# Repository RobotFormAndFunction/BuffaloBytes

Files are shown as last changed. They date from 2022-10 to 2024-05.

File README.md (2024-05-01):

## Outline
- [Overview](https://github.com/RobotFormAndFunction/BuffaloBytes/edit/main/README.md#overview)
- [Hardware Specifications](https://github.com/RobotFormAndFunction/BuffaloBytes/edit/main/README.md#hardware-specifications)
- [Hardware Assembly](https://github.com/RobotFormAndFunction/BuffaloBytes#assembly)
- [Programming](https://github.com/RobotFormAndFunction/BuffaloBytes#programming)

# Overview
This repository contains Buffalo Bytes design, including the circuit board and mechanical hardware. The bill of materials and 3D design files are included. This README file details the hardware specifications and tutorials on getting started with the Buffalo Bytes platform.

The robot is presented in the the IEEE Robotics and Automation Letter article, [Buffalo Byte: A Highly Mobile and Autonomous Millirobot Platform](https://ieeexplore.ieee.org/document/10465605)

To cite:
```bibtex
@ARTICLE{Singh_2024,
  author={Singh, Shashwat and Truax, Reed and St.~Pierre, Ryan},
  journal={IEEE Robotics and Automation Letters}, 
  title={Buffalo Byte: A Highly Mobile and Autonomous Millirobot Platform}, 
  year={2024},
  volume={9},
  number={5},
  pages={4067-4074},
  keywords={Robots;Robot sensing systems;Legged locomotion;Wheels;Batteries;Wireless fidelity;Three-dimensional displays;Biomimetics;field robots;biologically-inspired robots;millirobot},
  doi={10.1109/LRA.2024.3375290}}
```

# Hardware Specifications
This section details the electrical and mechanical hardware used in the Buffalo Bytes platform.

## Electrical hardware
The custom PCB for Buffalo Bytes is detailed in [here](https://github.com/RobotFormAndFunction/BuffaloBytes/tree/main/ElectricalHardware), with the schematic of the board, Gerber files, and BOM (bill of materials). The microcontroller is an ESP8266x SoC (system-on-a-chip), which enables Wi-Fi, and general input/outputs. The summary of electrical hardware is below in the BOM. 

<details><summary>Bill of materials (BOM)</summary>

#### Passives

| Component | Value	| Quantity | Package size |
| :--- | --- | :---: | --- |
| Capacitor |	0.1 µF |	5 |	0603 |
| Capacitor |	8.6 pF |	1 |	0603 |
| Capacitor | 2.4 pF |	1 |	0603 |
| Capacitor |	10 µF |	3 |	0603 |
| Capacitor |	1 µF |	2 |	0603 |
| Capacitor |	5.6 pF |	2 |	0603 |
| Capacitor |	2.2 µF |	1 |	0603 |
| Capacitor |	220 pF |	1 |	0603 |
| Capacitor |	0.01 µF |	1 |	0603 |		
| Inductor | 1.5 nH |	1 |	0603 |		
| Resistor |	200 Ω |	1 |	0603 |
| Resistor |	12 kΩ |	5 |	0603 |
| Resistor |	1 kΩ |	1 |	0603 |
| Resistor |	4.7 kΩ |	4 |	0603 |		
| LED |	Red |	1 |	0603 |

#### Electronics

| Part | Part Number	| Quantity | Package size |
| :--- | --- | :---: | --- |
| Antenna |	AN9520-245 |	1 |	ANT-SMD_L9.5-W2.1 |
| Crystal - 26 MHz | ECS-260 |	1 |	4-SMD, no lead |
| MCU |	ESP8266x |	1 |	QFN-32 |
| Motor driver |	DRV8833 |	1 |	TSSOP-16 |
| IMU |	MPU6050 |	1 |	QFN-24 |
| LDO Voltage regulator |	TPS7A0533PDBZR | 1 |	SOT-23 |	
| Flash memory | ZB25VQ80 | 1 | SOIC-8 |
</details>

# Assembly
The exploded view of a Buffalo Byte is shown below.

<p align="center">
Exploded View of Buffalo Bytes
</p>

First, the custom PCB needs to be populated (details in [Electrical Hardware](https://github.com/RobotFormAndFunction/BuffaloBytes/tree/main/ElectricalHardware)), and all of the mechanical hardware sourced, printed, and molded (details in [Mechanical Hardware](https://github.com/RobotFormAndFunction/BuffaloBytes/tree/main/MechanicalHardware)).

Each Buffalo Byte is assembled by sliding the motors into the chassis, attached the actuated wheels to the motors, and unactuated wheels to carbon fiber axles. The molded treads are wrapped around each actuated-unactuated wheel pair. The motor wires are connected to the custom PCB, and the battery connected to the PCB as well. Kapton tape is applied around the body to secure all parts. 

## Programming

To Buffalo Bytes Boards has 8 headers that goes directly into female headers of ESP8266 burning fixture to upload either the bootloader or code through serial communication. A USB-ASP programmer can also be used to do the same task, though the burning fixture is recommended. 

<p align="center">
ESP8266 Burning fixture
</p>

The board can be bootloaded with both Arduino and MicroPython to make software development easy. In this work, the board is flashed with the Arduino bootloader, and the Arduino IDE was used for software development. Alternatively, the board also enables wireless programming using Wi-Fi. To do this, a base script must be first uploaded through a serial connection, then additional programs can be sent via Wi-Fi.

To bootload Micropython firmware on the board, we downloaded and uploaded the latest micropython firmware from official micropython website. [(https://micropython.org/download/esp8266-1m/)](https://micropython.org/download/esp8266-1m/).

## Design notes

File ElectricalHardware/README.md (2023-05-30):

# Electrical hardware
The custom PCB of for Buffalo Bytes is shown below, with the top (A) and bottom (B). 

<p align="center">
PCB_annotate
</p>

The schematic of the board is shown [here](https://github.com/RobotFormAndFunction/BuffaloBytes/blob/main/ElectricalHardware/Buffalo_Bytes_schematic.pdf), and Gerber files [here](https://github.com/RobotFormAndFunction/BuffaloBytes/blob/main/ElectricalHardware/Gerber_PCB_BuffaloBytes.zip).

## Bill of materials (BOM)

### Passives

| Component | Value	| Quantity | Package size |
| :--- | --- | :---: | --- |
| Capacitor |	0.1 µF |	5 |	0603 |
| Capacitor |	8.6 pF |	1 |	0603 |
| Capacitor | 2.4 pF |	1 |	0603 |
| Capacitor |	10 µF |	3 |	0603 |
| Capacitor |	1 µF |	2 |	0603 |
| Capacitor |	5.6 pF |	2 |	0603 |
| Capacitor |	2.2 µF |	1 |	0603 |
| Capacitor |	220 pF |	1 |	0603 |
| Capacitor |	0.01 µF |	1 |	0603 |		
| Inductor | 1.5 nH |	1 |	0603 |		
| Resistor |	200 Ω |	1 |	0603 |
| Resistor |	12 kΩ |	5 |	0603 |
| Resistor |	1 kΩ |	1 |	0603 |
| Resistor |	4.7 kΩ |	4 |	0603 |		
| LED |	Red |	1 |	0603 |

### Electronics

| Part | Part Number	| Quantity | Package size |
| :--- | --- | :---: | --- |
| Antenna |	AN9520-245 |	1 |	ANT-SMD_L9.5-W2.1 |
| Crystal - 26 MHz | ECS-260 |	1 |	4-SMD, no lead |
| MCU |	ESP8266x |	1 |	QFN-32 |
| Motor driver |	DRV8833 |	1 |	TSSOP-16 |
| IMU |	MPU6881 |	1 |	QFN-24 |
| LDO Voltage regulator |	TPS7A0533PDBZR | 1 |	SOT-23 |	
| Flash memory | ZB25VQ80 | 1 | SOIC-8 |

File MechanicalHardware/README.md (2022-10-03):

# Mechanical hardware

The mechanical hardware of the Buffalo Bytes requires both commercial off-the-shelf (COTS) hardware and custom hardare. The COTS hardware is listed below in the bill of materials (BOM) and the STL files for the custom hardware in this repository. 

## COTS hardware
| Component| Quantity | Comment |
| :--- | :---: | --- |
| Two-stage (26:1) planetary gearmotor |	2 |	Available from Pololu |
| LiPo Battery (3.7 V @ 100 mAh) |	1 |	Available on Amazon |
| Carbon fiber rod | 1 | 1 mm diameter cut to size |
| Silicone polymer | 1 | DragonSkin 10 from Smooth-On |

## Custom hardware
One copy of the [chassis.stl](https://github.com/RobotFormAndFunction/BuffaloBytes/blob/main/MechanicalHardware/chassis.stl) and four copies of the [wheel.stl](https://github.com/RobotFormAndFunction/BuffaloBytes/blob/main/MechanicalHardware/wheel.stl) files need to be printed on an SLA printer. We used an AnyCubic Mono SE printer. The parts were printed according to the directions for the printer, and post-processed by rinsing with IPA, and cured in a UV light chamber. Other 3D printing options may require different processing.

The [tread_mold.stl](https://github.com/RobotFormAndFunction/BuffaloBytes/blob/main/MechanicalHardware/tread_mold.stl) file was printed on an FDM printer, we used a Raise3D E2 printer. After printing, a two-part silicone rubber (DragonSkin 10) was mixed and poured into the mold and allowed to cure overnight.

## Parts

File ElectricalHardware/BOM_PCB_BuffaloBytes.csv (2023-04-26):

ID | Name | Designator | Footprint | Quantity | Manufacturer Part | Manufacturer | Supplier | Supplier Part | Price | Pins | 3DModel | Contributor | Frequency | link
1 | 8.6pF | C2 | C0603 | 1 |  |  |  |  |  | 2 | C0603_L1.6-W0.8-H0.8 | LCEDA_Lib |  | https://item.szlcsc.com/362304.html
2 | 2.4pF | C3 | C0603 | 1 |  |  |  |  |  | 2 | C0603_L1.6-W0.8-H0.8 | LCEDA_Lib |  | https://item.szlcsc.com/362304.html
3 | 10u | C10 | C0603 | 1 |  |  |  |  |  | 2 | C0603_L1.6-W0.8-H0.8 | LCEDA_Lib |  | https://item.szlcsc.com/362304.html
4 | 1uF | C16 | C0603 | 1 |  |  |  |  |  | 2 | C0603_L1.6-W0.8-H0.8 | LCEDA_Lib |  | https://item.szlcsc.com/362304.html
5 | 200 | R1 | R0603 | 1 |  |  |  |  |  | 2 | R0603 | LCEDA_Lib |  | https://www.mouser.in/datasheet/2/447/PYu_RT_1_to_0_01_RoHS_L_11-1669912.pdf
6 | 12k | R2,R4,R6,R5,R7 | R0603 | 5 |  |  |  |  |  | 2 | R0603 | LCEDA_Lib |  | https://www.mouser.in/datasheet/2/447/PYu_RT_1_to_0_01_RoHS_L_11-1669912.pdf
7 | 1k | R3,R8,R9 | R0603 | 3 |  |  |  |  |  | 2 | R0603 | LCEDA_Lib |  | https://www.mouser.in/datasheet/2/447/PYu_RT_1_to_0_01_RoHS_L_11-1669912.pdf
8 | TPS7A0533PDBZR | U4 | SOT-23-3_L2.9-W1.3-P1.90-LS2.4-BR | 1 | TPS7A0533PDBZR | TI(德州仪器) | LCSC | C2877921 | 0.077 | 3 | SOT-23-3P_L2.9-W1.3-H1.0-LS2.4-P0.95 | LCSC |  | https://www.diodes.com/assets/Package-Files/SOT23.pdf
9 | 1.27MM*4P排母 | MO | HDR-TH_4P-P1.27_1.27MM-4P | 1 | 1.27mm*4P排母 |  | LCSC | C9900006150 |  | 4 | HDR-TH_4P-P1.27_1.27MM-4P | LCSC |  | https://cn.bing.com/search?q=datasheet： 1.27mm*4P排母
10 | Molex white 2-pin | J1 | MOLEX PICOBLADE 2P SMD | 1 | Molex white 2-pin |  |  |  |  | 4 |  | Dror
11 | 1.5nH | L1 | L0603 | 1 |  |  |  |  |  | 2 | L0603_L1.6-W0.8-H0.5_BEAD | LCEDA_Lib |  | https://item.szlcsc.com/344093.html
12 | AN9520-245 | L3 | ANT-SMD_L9.5-W2.1 | 1 | AN9520-245 | Rainsun | LCSC | C99665 | 0.05 | 2 | ANT-SMD_L9.5-W2.1-H1.0 | 立创EDA官方封装库 |  | https://item.szlcsc.com/100880.html
13 | LED-0603_R | LED1 | LED0603_RED | 1 | 19-217/R6C-AL1M2VY/3T | EVERLIGHT(台湾亿光) | LCSC | C72044 | 0.003 | 2 | LED0603_Red | LCEDA_01
14 | ESP8266EX | U1 | QFN-32_L5.0-W5.0-P0.50-BL-EP3.7 | 1 | ESP8266EX | ESPRESSIF | LCSC | C77967 | 0.167 | 33 | QFN-32_L5.0-W5.0-H0.8-P0.50-BL-EP3.7 | lcsc | 2.4GHz | https://item.szlcsc.com/18002.html
15 | W25Q32JWSSIQ_C2980995 | U2 | SOIC-8_L5.3-W5.3-P1.27-LS8.0-BL | 1 | W25Q32JWSSIQ | WINBOND(华邦) | LCSC | C2980995 | 0.124 | 8 | SOIC-8_L5.3-W5.3-H1.9-LS7.9-P1.27 | LCSC |  | https://atta.szlcsc.com/upload/public/pdf/source/20210417/916358944D87095CD419D96946FBE847.pdf
16 | 10pF | C12,C8 | C0603 | 2 |  |  |  |  |  | 2 | C0603_L1.6-W0.8-H0.8 | LCEDA_Lib |  | https://item.szlcsc.com/362304.html
17 | 26MHz | X2 | CRYSTAL-SMD_4P-L1.6-W1.2-BL | 1 | X1E000251001400 | EPSON(爱普生) | LCSC | C1985224 | 0.057 | 4 | CRYSTAL-SMD_4P-L1.6-W1.2-BL | LCSC |  | https://atta.szlcsc.com/upload/public/pdf/source/20180822/C255986_1A5575095A8CA427CA557DB66E6B870C.pdf
18 | Presa PCB HARWIN, 10 vie, 2 file, passo 1.27mm, Foro passante | U5 | HEADER PTR 10X1,27 | 1 | M50-3530842 | M50-3000545 | RS-Online | 681-0692 |  | 10 |  | Marco Anfesi |  | https://it.rs-online.com/web/p/prese-pcb/6810692
19 | 10nF | C11 | C0603 | 1 |  |  |  |  |  | 2 | C0603_L1.6-W0.8-H0.8 | LCEDA_Lib |  | https://item.szlcsc.com/362304.html
20 | 0.1u | C1,C4,C18,C19 | C0603 | 4 |  |  |  |  |  | 2 | C0603_L1.6-W0.8-H0.8 | LCEDA_Lib |  | https://item.szlcsc.com/362304.html
21 | 10k | R12,R14,R15,R16 | R0603 | 4 |  |  |  |  |  | 2 | R0603 | LCEDA_Lib |  | https://www.mouser.in/datasheet/2/447/PYu_RT_1_to_0_01_RoHS_L_11-1669912.pdf
22 | MPU-6881_C468935 | R13 | QFN-24_L3.0-W3.0-P0.40-TL-EP | 1 | MPU-6881 | TDK InvenSense(应美盛) | LCSC | C468935 | 0.588 | 25 |  | LCSC |  | http://file1.dzsc.com/product/15/01/20/193739_103049784.pdf
23 | 10uF | C5,C17 | C0603 | 2 |  |  |  |  |  | 2 | C0603_L1.6-W0.8-H0.8 | LCEDA_Lib |  | https://item.szlcsc.com/362304.html
24 | 1u | C6 | C0603 | 1 |  |  |  |  |  | 2 | C0603_L1.6-W0.8-H0.8 | LCEDA_Lib |  | https://item.szlcsc.com/362304.html
25 | 2.2u | C9 | C0603 | 1 |  |  |  |  |  | 2 | C0603_L1.6-W0.8-H0.8 | LCEDA_Lib |  | https://item.szlcsc.com/362304.html
26 | 0.01u | C15 | C0603 | 1 |  |  |  |  |  | 2 | C0603_L1.6-W0.8-H0.8 | LCEDA_Lib |  | https://item.szlcsc.com/362304.html
27 | DRV8833CPWPR | U3 | TSSOP-16_L5.0-W4.4-P0.65-LS6.4-BL-EP-1 | 1 | DRV8833CPWPR | Texas Instruments | LCSC | C191171 | 0.868 | 17 | TSSOP-16_L5.0-W4.4-P0.65-LS6.4-BL-EP-1 | LCSC |  | https://www.ti.com/cn/lit/ds/symlink/drv8833c.pdf?ts=1631004531499

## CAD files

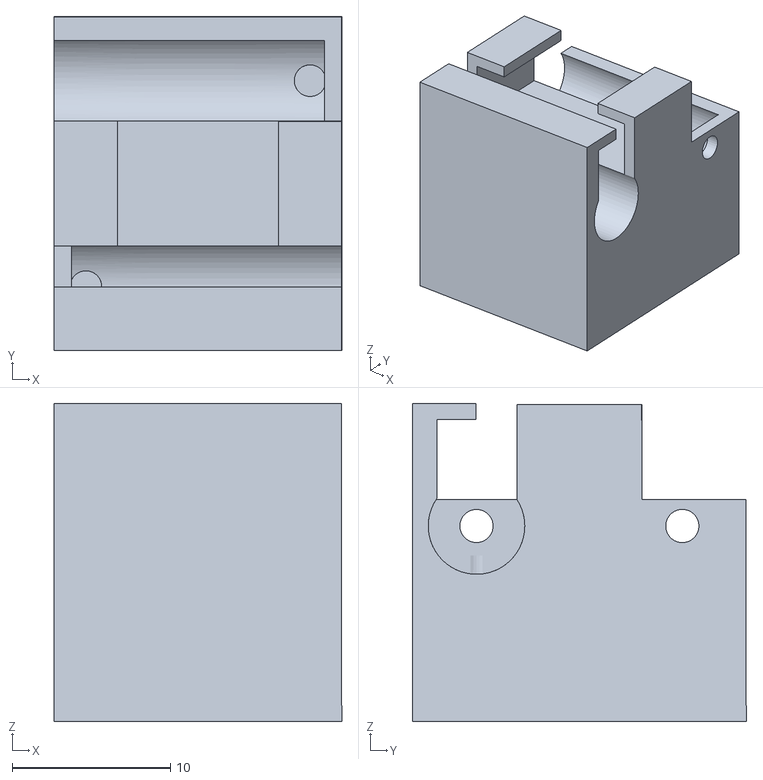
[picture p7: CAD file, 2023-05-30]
MechanicalHardware/NewChassis.stl
18.2 x 21.1 x 20.1

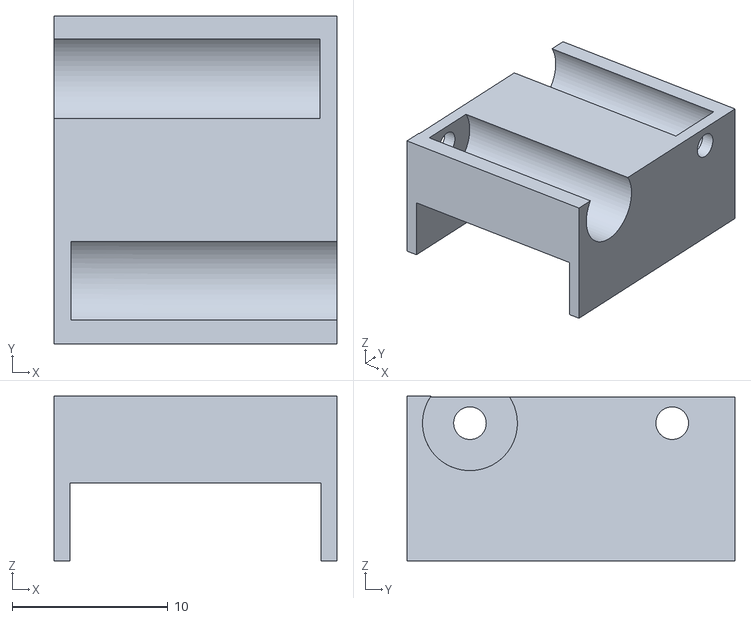
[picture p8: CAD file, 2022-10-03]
MechanicalHardware/chassis.stl
18.2 x 21.1 x 10.6

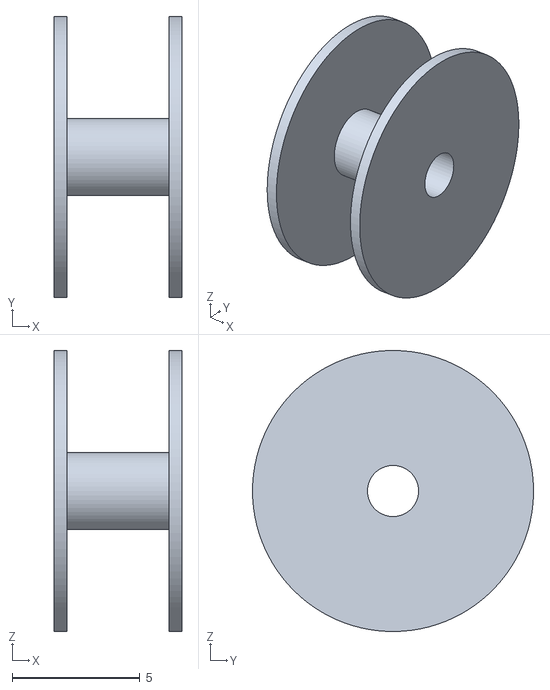
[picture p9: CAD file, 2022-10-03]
MechanicalHardware/wheel.stl
5.00 x 11.0 x 11.0

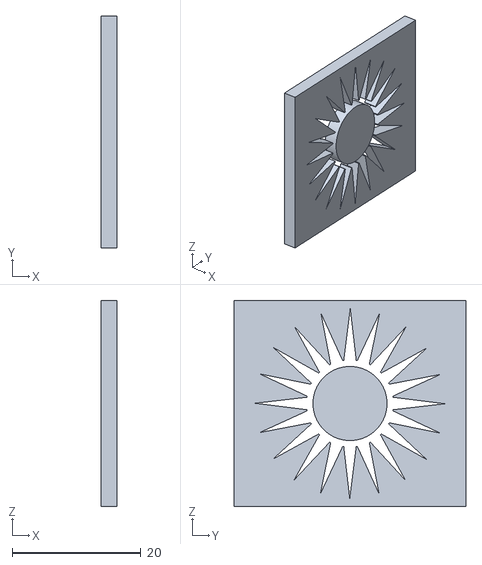
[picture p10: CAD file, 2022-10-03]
MechanicalHardware/tread_mold.stl
2.50 x 36.0 x 32.0

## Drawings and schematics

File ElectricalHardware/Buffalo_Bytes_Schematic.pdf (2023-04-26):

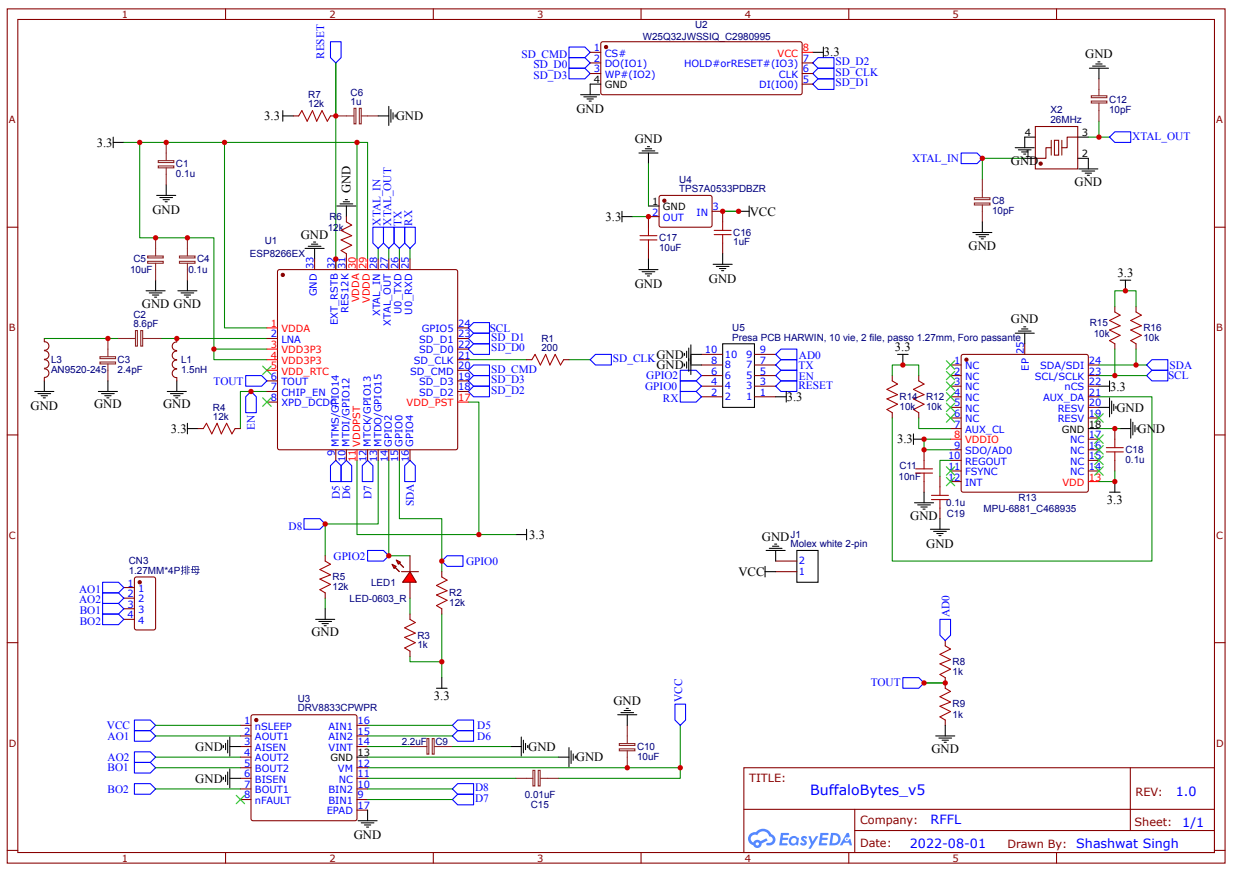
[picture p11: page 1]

Drawn By: Shashwat Singh

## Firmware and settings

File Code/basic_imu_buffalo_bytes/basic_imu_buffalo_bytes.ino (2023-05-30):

/***************************************************************************
* Example sketch for the MPU6500_WE library
*
* This sketch shows how to get acceleration, gyroscocope and temperature 
* data from the MPU6500. In essence, the difference to the MPU9250 is the
* missing magnetometer. The shall only show how to "translate" all other 
* MPU9250 example sketches for use of the MPU6500
* 
* For further information visit my blog:
*
* https://wolles-elektronikkiste.de/mpu9250-9-achsen-sensormodul-teil-1  (German)
* https://wolles-elektronikkiste.de/en/mpu9250-9-axis-sensor-module-part-1  (English)
* 
***************************************************************************/

#include <MPU6500_WE.h>
#include <Wire.h>
#define MPU6500_ADDR 0x69

/* There are several ways to create your MPU6500 object:
 * MPU6500_WE myMPU6500 = MPU6500_WE()              -> uses Wire / I2C Address = 0x68
 * MPU6500_WE myMPU6500 = MPU6500_WE(MPU6500_ADDR)  -> uses Wire / MPU6500_ADDR
 * MPU6500_WE myMPU6500 = MPU6500_WE(&wire2)        -> uses the TwoWire object wire2 / MPU6500_ADDR
 * MPU6500_WE myMPU6500 = MPU6500_WE(&wire2, MPU6500_ADDR) -> all together
 * Successfully tested with two I2C busses on an ESP32
 */
MPU6500_WE myMPU6500 = MPU6500_WE(MPU6500_ADDR);

void setup() {
  Serial.begin(115200);
  Wire.begin();
  if(!myMPU6500.init()){
    Serial.println("MPU6500 does not respond");
  }
  else{
    Serial.println("MPU6500 is connected");
  }
  
  /* The slope of the curve of acceleration vs measured values fits quite well to the theoretical 
   * values, e.g. 16384 units/g in the +/- 2g range. But the starting point, if you position the 
   * MPU6500 flat, is not necessarily 0g/0g/1g for x/y/z. The autoOffset function measures offset 
   * values. It assumes your MPU6500 is positioned flat with its x,y-plane. The more you deviate 
   * from this, the less accurate will be your results.
   * The function also measures the offset of the gyroscope data. The gyroscope offset does not   
   * depend on the positioning.
   * This function needs to be called at the beginning since it can overwrite your settings!
   */
  Serial.println("Position you MPU6500 flat and don't move it - calibrating...");
  delay(1000);
  myMPU6500.autoOffsets();
  Serial.println("Done!");
  
  /*  This is a more accurate method for calibration. You have to determine the minimum and maximum 
   *  raw acceleration values of the axes determined in the range +/- 2 g. 
   *  You call the function as follows: setAccOffsets(xMin,xMax,yMin,yMax,zMin,zMax);
   *  Use either autoOffset or setAccOffsets, not both.
   */
  //myMPU6500.setAccOffsets(-14240.0, 18220.0, -17280.0, 15590.0, -20930.0, 12080.0);

  /*  The gyroscope data is not zero, even if you don't move the MPU6500. 
   *  To start at zero, you can apply offset values. These are the gyroscope raw values you obtain
   *  using the +/- 250 degrees/s range. 
   *  Use either autoOffset or setGyrOffsets, not both.
   */
  //myMPU6500.setGyrOffsets(45.0, 145.0, -105.0);

  /*  You can enable or disable the digital low pass filter (DLPF). If you disable the DLPF, you 
   *  need to select the bandwdith, which can be either 8800 or 3600 Hz. 8800 Hz has a shorter delay,
   *  but higher noise level. If DLPF is disabled, the output rate is 32 kHz.
   *  MPU6500_BW_WO_DLPF_3600 
   *  MPU6500_BW_WO_DLPF_8800
   */
  myMPU6500.enableGyrDLPF();
  //myMPU6500.disableGyrDLPF(MPU6500_BW_WO_DLPF_8800); // bandwdith without DLPF
  
  /*  Digital Low Pass Filter for the gyroscope must be enabled to choose the level. 
   *  MPU6500_DPLF_0, MPU6500_DPLF_2, ...... MPU6500_DPLF_7 
   *  
   *  DLPF    Bandwidth [Hz]   Delay [ms]   Output Rate [kHz]
   *    0         250            0.97             8
   *    1         184            2.9              1
   *    2          92            3.9              1
   *    3          41            5.9              1
   *    4          20            9.9              1
   *    5          10           17.85             1
   *    6           5           33.48             1
   *    7        3600            0.17             8
   *    
   *    You achieve lowest noise using level 6  
   */
  myMPU6500.setGyrDLPF(MPU6500_DLPF_6);

  /*  Sample rate divider divides the output rate of the gyroscope and accelerometer.
   *  Sample rate = Internal sample rate / (1 + divider) 
   *  It can only be applied if the corresponding DLPF is enabled and 0<DLPF<7!
   *  Divider is a number 0...255
   */
  myMPU6500.setSampleRateDivider(5);

  /*  MPU6500_GYRO_RANGE_250       250 degrees per second (default)
   *  MPU6500_GYRO_RANGE_500       500 degrees per second
   *  MPU6500_GYRO_RANGE_1000     1000 degrees per second
   *  MPU6500_GYRO_RANGE_2000     2000 degrees per second
   */
  myMPU6500.setGyrRange(MPU6500_GYRO_RANGE_250);

  /*  MPU6500_ACC_RANGE_2G      2 g   (default)
   *  MPU6500_ACC_RANGE_4G      4 g
   *  MPU6500_ACC_RANGE_8G      8 g   
   *  MPU6500_ACC_RANGE_16G    16 g
   */
  myMPU6500.setAccRange(MPU6500_ACC_RANGE_2G);

  /*  Enable/disable the digital low pass filter for the accelerometer 
   *  If disabled the bandwidth is 1.13 kHz, delay is 0.75 ms, output rate is 4 kHz
   */
  myMPU6500.enableAccDLPF(true);

  /*  Digital low pass filter (DLPF) for the accelerometer, if enabled 
   *  MPU6500_DPLF_0, MPU6500_DPLF_2, ...... MPU6500_DPLF_7 
   *   DLPF     Bandwidth [Hz]      Delay [ms]    Output rate [kHz]
   *     0           460               1.94           1
   *     1           184               5.80           1
   *     2            92               7.80           1
   *     3            41              11.80           1
   *     4            20              19.80           1
   *     5            10              35.70           1
   *     6             5              66.96           1
   *     7           460               1.94           1
   */
  myMPU6500.setAccDLPF(MPU6500_DLPF_6);

  /* You can enable or disable the axes for gyroscope and/or accelerometer measurements.
   * By default all axes are enabled. Parameters are:  
   * MPU6500_ENABLE_XYZ  //all axes are enabled (default)
   * MPU6500_ENABLE_XY0  // X, Y enabled, Z disabled
   * MPU6500_ENABLE_X0Z   
   * MPU6500_ENABLE_X00
   * MPU6500_ENABLE_0YZ
   * MPU6500_ENABLE_0Y0
   * MPU6500_ENABLE_00Z
   * MPU6500_ENABLE_000  // all axes disabled
   */
  //myMPU6500.enableAccAxes(MPU6500_ENABLE_XYZ);
  //myMPU6500.enableGyrAxes(MPU6500_ENABLE_XYZ);
  delay(200);
}

void loop() {
  xyzFloat gValue = myMPU6500.getGValues();
  xyzFloat gyr = myMPU6500.getGyrValues();
  float temp = myMPU6500.getTemperature();
  float resultantG = myMPU6500.getResultantG(gValue);

  Serial.println("Acceleration in g (x,y,z):");
  Serial.print(gValue.x);
  Serial.print("   ");
  Serial.print(gValue.y);
  Serial.print("   ");
  Serial.println(gValue.z);
  Serial.print("Resultant g: ");
  Serial.println(resultantG);

  Serial.println("Gyroscope data in degrees/s: ");
  Serial.print(gyr.x);
  Serial.print("   ");
  Serial.print(gyr.y);
  Serial.print("   ");
  Serial.println(gyr.z);

  Serial.print("Temperature in °C: ");
  Serial.println(temp);

  Serial.println("********************************************");

  delay(1000);
}

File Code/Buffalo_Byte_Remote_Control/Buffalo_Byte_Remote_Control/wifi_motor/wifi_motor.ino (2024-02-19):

#include <ESP8266WiFi.h>
#include <WiFiClient.h>
#include <ESP8266WebServer.h>

// Replace with your network credentials
const char* ssid = "Aniket";         
const char* password = "1234567890";

ESP8266WebServer server(80);   //instantiate server at port 80 (http port)

String page = ""; //For the Web Server
String page2="";  //For updating Status of motor 1
String page3="";  //For updating status of motor 2
void setup(void)
{
  //the HTML of the web page
  page = "<center><h1>Motor Control Web Server</h1><body><p><a href=\"Forward\"><button>Forward</button></a><p><a href=\"Backward\"><button>Backward</button></a></p><p><a href =\"Left\"><button>Left</button></a>&nbsp;<a href=\"Stop\"><button>Stop</button></a><a href=\"Right\"><button>Right</button></a></p></body></center>";
  pinMode(14, OUTPUT);   // inputs for motor 1
  pinMode(12,OUTPUT);
  pinMode(13,OUTPUT);    // inputs for motor 2 
  pinMode(15,OUTPUT);
  pinMode(LED_BUILTIN,OUTPUT);  // For status of WiFi connection
  delay(1000);
  Serial.begin(115200);     
  WiFi.begin(ssid, password); //begin WiFi connection
  Serial.println("");

  // Wait for connection
  while (WiFi.status() != WL_CONNECTED) {
    delay(500);
    Serial.print(".");
  }
  digitalWrite(LED_BUILTIN,HIGH);     // when connected turns high
  Serial.println("");
  Serial.print("Connected to ");   
  Serial.println(ssid);
  Serial.print("IP address: ");
  Serial.println(WiFi.localIP());   //provides IP address
   server.on("/", [](){
    server.send(200, "text/html", page+page2);
  });
  server.on("/Forward",Forward);
  server.on("/Backward",Backward);
  server.on("/Left",Left);
  server.on("/Right",Right);

  server.on("/Stop",[](){                              // turns all the motor input pins low
   page2="<center><p> motor 1 Status : Off</p></center>";
   page3="<center><p> motor 2 Status : off</p></center>";
  server.send(200,"text/html",page+page2+page3);
    digitalWrite(14,LOW);
    digitalWrite(12,LOW);
    digitalWrite(13,LOW);
    digitalWrite(15,LOW);
    delay(200);
  });
  server.begin();
  Serial.println("Web server started!");
}
void loop(void)
{  
     server.handleClient();
}

 void Forward() 
 {
    analogWrite(14, 180);
    digitalWrite(12,LOW);
    digitalWrite(13,HIGH);
    digitalWrite(15,LOW);
    // digitalWrite(14,HIGH);

    page2="<center><p> motor 1 Status : Forward </p></center>";
    server.send(200,"text/html", page+page2+page3);
    delay(200);
  }
  void Left()
  {
    page3="<center><p> motor 2 Status : Left</p></center>";
    server.send(200,"text/html",page+page2+page3);

    analogWrite(14, 150);
    // digitalWrite(14,HIGH);
    digitalWrite(12,LOW);
    // digitalWrite(13,LOW);
    analogWrite(13, 150);
    digitalWrite(15,HIGH);

    delay(200);
  }
  void Right()
   { 
    page3="<center><p> motor 2 Status : Right</p></center>";
    server.send(200,"text/html",page+page2+page3);
    digitalWrite(14,LOW);
    digitalWrite(12,HIGH);
    analogWrite(13, 150);
    digitalWrite(15,LOW);
    delay(200);
  }
   void Backward()
  {
    page2="<center><p> motor 1 Status : Backward</p></center>";
    server.send(200, "text/html", page+page2+page3);
    digitalWrite(14,LOW);
    digitalWrite(12,HIGH);
    digitalWrite(13,LOW);
    digitalWrite(15,HIGH);
    delay(200); 
  }

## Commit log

2022-01-25 adding in boards
2022-09-25 Uploaded the schematic
    Schematic for Buffalo Bytes
2022-09-25 uploaded Gerber files
    Gerber files for 4-layer Buffalo Bytes PCB
2022-10-03 STL files for mechanical hardware
    [chassis.stl, tread_mold.stl, wheel.stl]
2022-10-28 Upload schematic
2023-04-26 updated electronics files
    [BOM_PCB_BuffaloBytes.csv, PickAndPlace_PCB_BuffaloBytes.csv]
2023-04-26 updated electrical schematic
2024-02-19 Uploading the XCode Code for remote control
    The museum prototype remote control
2024-02-19 Arduino Remote control server
2024-04-26 IOS app updated with better UI
    - Dark mode and light mode switch
    - mutitouch functionality
